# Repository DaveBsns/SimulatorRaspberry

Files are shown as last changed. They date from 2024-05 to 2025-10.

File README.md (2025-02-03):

# VR Bicycle Simulator Repository (HHN UniTyLab)

This Repo contains all Scripts to run the VR Bicylce Simulator in addtion to the Unity Project. 

## Hardware Sensor Overview

// IMAGE FROM BIKE SETUP

### Steering Sensor

<div style="display: flex; justify-content: space-evenly; align-items: center;">
  Steering Sensor Mount
  Handle Bar Mount
</div>

The image on the left shows the mount of the Photoelelectrical Encoder to measure the steering angle - the right images shows the handle bar from the front. There are two boxes on the top of the handle bar. In this image the left box contains the Mircocontroller (ESP32) for the brake and the right box contains the Microcontroller (ESP32) for the Steering sensor.

### Brake Sensor

<div style="display: flex; justify-content: space-evenly; align-items: center;">
  Steering Sensor Mount
  Handle Bar Mount
  Handle Bar Mount
</div>

Currently only the right hand brake is equipped with a sensor. The full setup is shown on the left image. The center images shows the mount of the hall sensor on the brake lever. If the brake sticks or does not work properly - make sure to check both screws are tight. 
The image on the right show the brake-block mounted in the V-brake - this block ensures a more realistc feeling of the brake lever.

**Important:** Make sure that the LED-light of the switch of the box is On - otherwise the brake sensor will be running with an older version!

### Elite Rizer

<div style="display: flex; justify-content: space-evenly; align-items: center;">
  Steering Sensor Mount
</div>

The Elite Rizer is used to adjust the height of the front axis occording to the incline in the Simulation. Be aware that this component needs to find the Zero points when being started.

### Direto 

<div style="display: flex; justify-content: space-evenly; align-items: center;">
  Steering Sensor Mount
</div>

This component is responsible for measuring the speed of the pedals and adjusting the resistance of the pedals accourding to the incline in the simulation. 

### Roll 

<div style="display: flex; justify-content: space-evenly; align-items: center;">
  Steering Sensor Mount
</div>

This (white) roll can be used to move backwards with the bicycle in the simulation. To go backwards the roll has to be kicked forwards.

## Repository Overview

- **`archive/`**: Archived files and scripts.
  
- **`collector_scripts/`**: Main directory for scripts handling data collection and Sensor scripts.
  
  - **`sensor_scripts/`**: Each Subdirectory contains a PlatformIO project - one for each mircocontroller (ESP32) utilising a sensor for data collection of the Bicycle setup. 

    - **`Arduino_Files/`** ---
    - **`Brake_Sensor/`** Hall sensor mounted on left brake lever (indirect brake force)
    - **`Gyro_Sensor/`** BNO055 mounted on Rocker plate (measure tilting)
    - **`Roll_Sensor/`** Roll sensor (for backward movement on bicycle)
    - **`Steering_Sensor/`** Photoelectric encoder (steering Angle)

  - `direto_xr.py` Script utilising BLE for reading speed from direto and writing resitance of direto
  - `elite_rizer.py` Script utilising BLE for writing front wheel height
  - `headwind.py` Script utilising BLE for writing headwind speed
  - `master_collector.py` Scripct for collecting data from microcontrollers (UDP) and sending data to Unity (UDP)
  - `master_receiver.py` Script for recieving data from Unity (UDP)
  - `p110_connect.py` Script for controlling smart plug (power supply for bicycle setup)
  - `UDP_tester.py` Srcipt for testing UDP functionality
  - `run_scripts.bat`: Batch script for running all scripts.

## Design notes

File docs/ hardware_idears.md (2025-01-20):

- Foot sensor while stand still Structure-borne sound transducer maybe with light barrier or pressure sensor
- Structure-borne sound transducer for undergound feedback and crashes (rockhorn)
- Brake feedback (maybe with pressure sensor)

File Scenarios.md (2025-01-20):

# Scenarios Bicycle Simulator

Parts of several use cases are combined into a scenario.

Scenario 1: Easy ride in the city
* Good weather
* Bicycle lane is free
* Cars keep their distance
* Cars don’t drive too fast
* Intersection with a red light that the cyclist crosses straight 
* Stop sign at intersection with traffic lights
* During the day
* Covers 15 Use Case Actions

Scenario 1b: Cycling on inclined slopes
* Ride in the parking garage
* no use case, just to test the Elite Rizer

Scenario 2: Difficult ride in the city
* Good weather
* Construction site on the bicycle lane
* Cars blocking the bicycle lane
* Fast traffic and close cars passes
* High traffic density
* Left turn incl. turning lane and traffic light
* Intersection without traffic lights and „Vorfahrt gewähren“ sign
* Zebrastreifen (Pedestrian crossing)
* Sun sets
* Covers 18 Use Case Actions

Scenario 3: Dangerous ride in the city
* Obstacles on the ground, narrow points
* Slow cyclists
* Cars drive fast and way too close
* Bad parking
* There is a „Vorfahrt“ intersection, but a car takes the right of way
* Covers 5 Use Case Actions

Scenario 4: Foggy night ride in the city
* Nighttime with lantern lights
* Cars pass by with headlights on
* Fog makes vision difficult
* Covers 6 Use Case Actions

Scenario 5: Adventure ride in the forest
* Hilly terrain
* Fog
* Forest
* Covers 4 Use Case Actions

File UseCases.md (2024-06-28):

# Use Cases Bicycle Simulator

## Use Case Overview

R1 - Removing barriers and building security

R2 - Expansion of driving practice (mainly on intersections)

R3 - Expansion of driving practice (mainly overtaking and narrow spots)

R4 - Expansion of driving practice at different times of the day

R5 - Weather influences when cycling

A1 - Building confidence on the bicycle path next to the road

A2 - Building confidence when driving on the road

A3.1 - Feeling safe when being overtaken by cars

A3.2 - Measuring stress when being overtaken by cars

A4 - Cycling at night and sharing the road with other cars

A5 - Cycling under varying weather conditions at varying times of day and at night

The individual cyclist actions are taken from the requirements document and named in alphabetical order.

## R1 - Removing barriers and building security

| Use Case Number | Description | Scenario | Direto | Rocker Plate | Brake | Rizer |
| --- | --- | --- | --- | --- | ----- | ----- |
| R1a | Getting on the bike | 1 | | x | | |
| R1b | Starting to ride the bike straight on even ground, no vehicles driving past | 1 | x | | | |
| R1b | Raising the right hand to indicate an upcoming turn to the right | 1 | x | x | | |
| R1b | Turning right | 2 | x | x | | |
| R1c | Raising the left hand to indicate an upcoming turn to the left | 2 | x | x | | |
| R1c | Turning left | 2 | x | x | | |
| R1d | Driving uphill | 5 | x | | | x |
| R1d | Driving downhill | 5 | x | | (x) | x |
| R1e | Riding around obstacle on the floor | 3 | x | x | | |
| R1f | Hitting the brakes hard because of a dangerous situation | 3 | | | x | |

## R2 - Expansion of driving practice (mainly on intersections)

| Use Case Number | Description | Scenario | Direto | Rocker Plate | Brake | Rizer |
| --- | --- | --- | --- | --- | ----- | ----- |
| R2a | Cyclist starts riding at an intersection | 1 | x | | | |
| R2b | Cyclist stops for a red traffic light | 1 | | | x | |
| R2c | Right turn indication and execution at an intersection | 2 | x | x | | |
| R2c | Left turn indication and execution at an intersection | 2 | x | x | | |
| R2d | Getting into the turning lane | 2 | x | x | x | |
| R2e | Traffic signs at intersections: Stop, Vorfahrt, Vorfahrt gewähren | 1/2/3 | x | | x | |

##

## R3 - Expansion of driving practice (mainly overtaking and narrow spots)

| Use Case Number | Description | Scenario | Direto | Rocker Plate | Brake | Rizer |
| --- | --- | --- | --- | --- | ----- | ----- |
| R3a | Driving past parked car (regular parking) | 1 | x | | | |
| R3a | Driving past parked car (bad parking going into the bicycle lane) | 2 | | | x | |
| R3b | Overtaking other cyclists | 3 | x | x | | |
| R3c | Driving through a narrow point | 3 | x | (x) | (x) | |

## R4 - Expansion of driving practice at different times of the day

| Use Case Number | Description | Scenario | Direto | Rocker Plate | Brake | Rizer |
| --- | --- | --- | --- | --- | ----- | ----- |
| R4a | Driving at dusk | 2 | x | | | |
| R4b | Driving during the night | 4 | x | | | |

## R5 - Weather influences when cycling

| Use Case Number | Description | Scenario | Direto | Rocker Plate | Brake | Rizer |
| --- | --- | --- | --- | --- | ----- | ----- |
| R5a | Driving on wet road | - | x | | | |
| R5b | Driving in rain | - | x | | | |
| R5b | Driving in fog | 4 | x | | | |
| R5c | Driving in snow and slippery conditions | - | x | x | | |
| R5c | Driving in snow and slippery conditions on a bridge | - | x | x | | |
| R5d | Braking for an obstacle visible only late because of bad weather conditions | 5 | | | x | |
| R5d | Braking in slippery weather conditions | - | | x | x | |
| R5e | Driving at night —> see no difference to R4b | 4 | x | | | |
| R5f | Driving in the city with poor visibility | 4 | x | | | |
| R5f | Driving in the forest with poor visibility | 5 | x | | | |

## A1 - Building confidence on the bicycle path next to the road

| Use Case Number | Description | Scenario | Direto | Rocker Plate | Brake | Rizer |
| --- | --- | --- | --- | --- | ----- | ----- |
| A1a | Being overtaken by passing cars in low traffic density | 1 | x | | | |
| A1a | Being overtaken by passing cars in high traffic density | 2 | x | | | |
| A1b | Being overtaken by passing cars with low speed | 1 | x | | | |
| A1b | Being overtaken by passing cars with high speed | 2 | x | | | |
| A1c | Crossing an intersection with low traffic density and traffic lights | 1 | x | | x | |
| A1c | Crossing an intersection with high traffic density and regular road crossing | 2 | x | | x | |

##

## A2 - Building confidence when driving on the road

| Use Case Number | Description | Scenario | Direto | Rocker Plate | Brake | Rizer |
| --- | --- | --- | --- | --- | ----- | ----- |
| A2a | Driving on the road, no bike path, low traffic density, slow cars | 1 | x | | | |
| A2a | Driving on the road, no bike path, high traffic density, fast cars | 2 | x | | | |
| A2bde | Approaching an intersection with cars, right turn incl. turning lane | 1 | x | x | x | |
| A2bde | Approaching an intersection with cars, left turn incl. turning lane  | 2 | x | x | x | |
| A2c | Stopping at traffic lights | 1 | | | x | |

##

## A3.1 - Feeling safe when being overtaken by cars

| Use Case Number | Description | Scenario | Direto | Rocker Plate | Brake | Rizer |
| --- | --- | --- | --- | --- | ----- | ----- |
| A3a | Being overtaken by a car with usual distance | 1 | x | | | |
| A3a | Being overtaken by a close car | 2 | x | | | |
| A3b | Being overtaken by a slow car (combine with A2a) | 1 | x | | | |
| A3b | Being overtaken by a fast car (combine with A2a) | 2 | x | | | |
| A3c | Being overtaken by a fast car with obstacles on the side | 2 | x | | x | |

##

## A4 - Cycling at night and sharing the road with other cars

| Use Case Number | Description | Scenario | Direto | Rocker Plate | Brake | Rizer |
| --- | --- | --- | --- | --- | ----- | ----- |
| A4a | Driving at dusk with car headlights behind you or in oncoming traffic  | 2 | x | | | |
| A4b | Driving at night with car headlights behind you or in oncoming traffic | 4 | x | | | |

##

## A5 - Cycling under varying weather conditions at varying times of day and at night

| Use Case Number | Description | Scenario | Direto | Rocker Plate | Brake | Rizer |
| --- | --- | --- | --- | --- | ----- | ----- |
| A5a | Driving on a wet road with cars next to it | - | x | | | |
| A5b | Driving in rain/fog or poor visibility including car headlights | 4 | x | | | |
| A5c | Driving in snow and slippery conditions, possibly with splashing slush | - | x | | | |
| A5d | Driving in different weather conditions at dusk and at night | - | x | | | |

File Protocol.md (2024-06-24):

Thursday, 21st March 2024:
- We're going to use a Miroboard for brainstorming (PB)
- Github issues for Task management
- Markdown for documentation
- Road runner license (DF)
- Demo: Booting up the simulator in the lab (DF)
- Basic workflow - work on the personal laptop, push the code, test in the lab, then merge successfully implemented features (DF)

Thursday, 28th March 2024:
- Determine whether to use Roadrunner or just Unity for VR editing using the following questions
1. What looks better?
2. What's easier to implement?
3. Do we have German roads, street signs and bicycle lanes?
- Overview of Unity version control
- Overview of sensor collection scripts
- Discussion of the steering logic: can be improved, but this isn't required in this project

Thursday, 11th April 2024:
- Preparation for intermediate presentation scheduled for April 18

Monday, 6th of May 2024:
- Pooja is working on lighting during the day
- Philipp Baumann is working on traffic lights
- Philipp Senfft is working on the Rizer
- Marc Hessenauer is working on the cars
- sync for presentation on May 16th
- agreement on parking garage as the next test area for incline
- agreement on slight adaption of the scenarios 2,3 and 4
- discussion on whether we will write a paper or a non-scientific documentation

Thu, 30 May 2024

Current State Overview
- Scenario 1: Complete and functional.
- Scenario 1b: Implementation on Unity side is complete; testing on the simulator is pending.
- Scenario 2 & 3 Concepts: Conceptualization is complete.
- Scenario 3: Philipp has begun implementation in Unity.
- Scenario 2: Pooja has begun implementation in Unity.

Goal for End of Semester
- Scenario 1: Ensure it is fully functional, including Scenario 1b to demonstrate a working Rizer.
- Scenario 2: Complete implementation, excluding weather conditions.
- Scenario 3: Complete implementation, excluding weather conditions and limited to basic physics for slow bicyclists.
- Documentation: Prepare and possibly finalize a paper or documentation of the project.

Thu, 6 June 2024: 

Current State Overview:
- Scenario 1: Complete & functional
- Scenario 1b: Work in Progress: Demonstraiting Incline (ajust Rizer)
- Scenario 2: (no new update because pooja could not attend meeting)
- Scenario 3: Scenario in Unity created with assets (wip: way point bike controller & missing: car takes the right of way)

Goal for End of Semester (27.6): 
- same goals as from 30 May 2024
- additional adjust the durito for incline demonstation
- Documentation: Write documentation of the project (not paper) until 5.7, latest 26.7.

Thu, 13 June 2024:
  
  Scenario 2: Work in Progress
  
  Scenario 3:
    - Done: WayPointBike slow self driving on bike lane
    - Work in Progress: Cars taking right of way
  
  Rizer: 
    - issue: DataReceiver has inconsistent values in calls variables.
  
  Documentaion:
    - inital draft of Structure missing additional Chapter of Project Structure (For others to know how to work on project in the future)
    
  Presentation: 
    - Goal 15 minutes (max 20 with demonstration)
    - Marc will create inital draft of presentation until next week

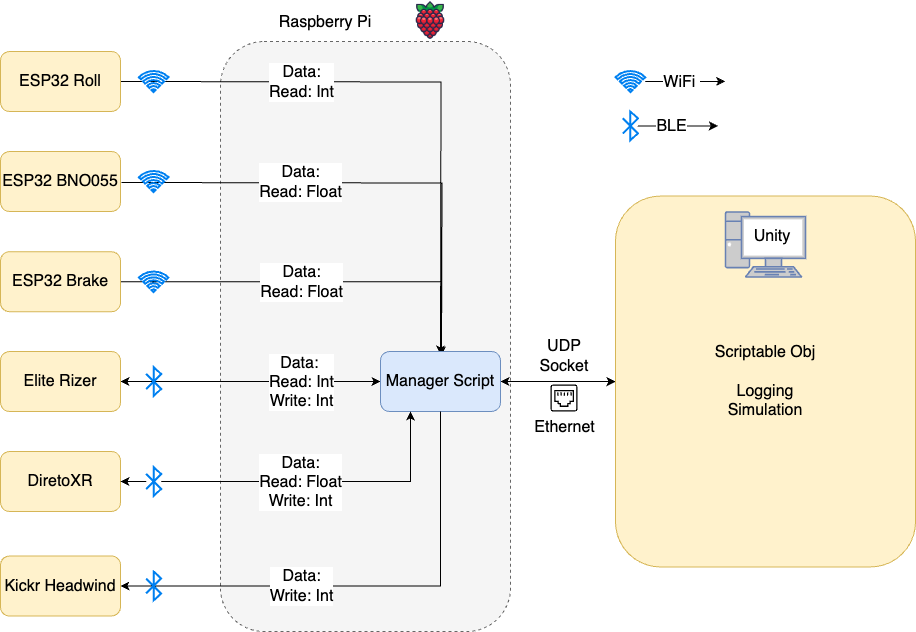
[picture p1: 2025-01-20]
Architecture_BicycleSimulator.drawio.png

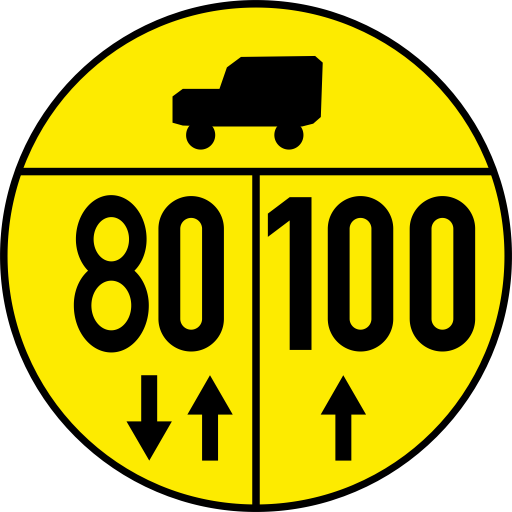
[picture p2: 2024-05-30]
roadrunner/signs/special_signs/Sign_I_1.png

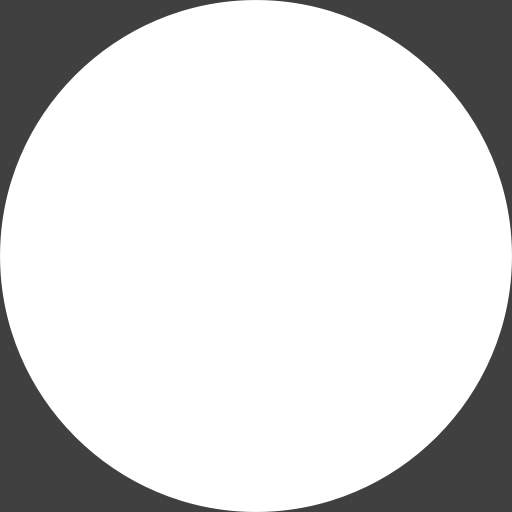
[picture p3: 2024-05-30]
roadrunner/signs/special_signs/Sign_I_1-Back.png

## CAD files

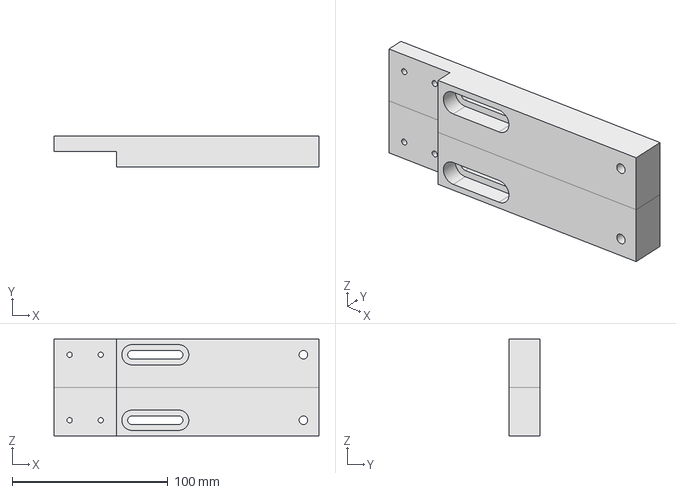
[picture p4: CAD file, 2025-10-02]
hardware/backward_motion_input/baseB.FCStd
170.0 x 20.0 x 62.0 mm

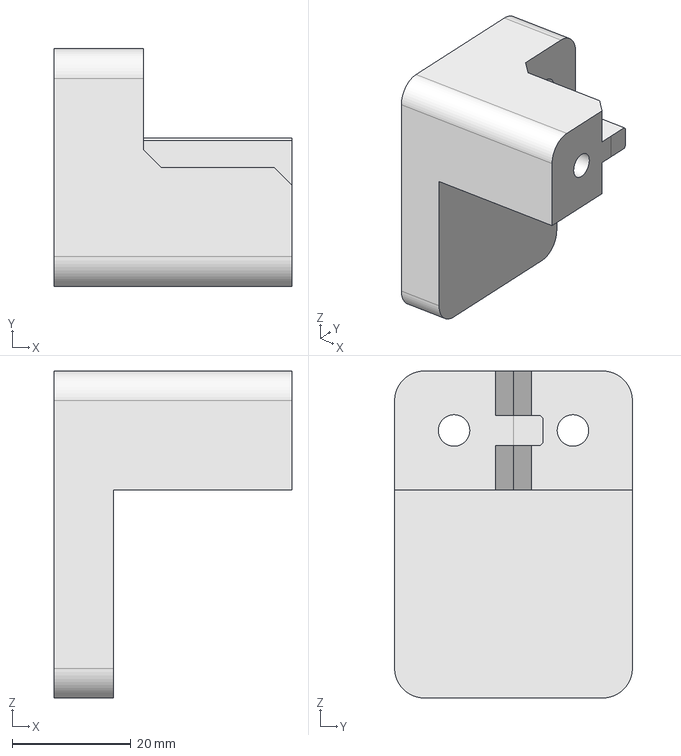
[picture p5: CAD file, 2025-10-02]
hardware/backwheel_and_pedal_sensor/backwheel_sensor_mount/clampJawA.FCStd
40.0 x 40.0 x 55.0 mm

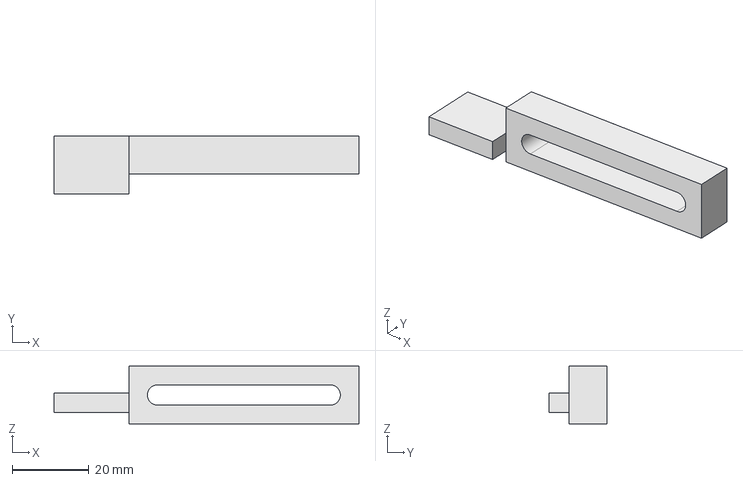
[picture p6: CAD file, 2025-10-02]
hardware/backwheel_and_pedal_sensor/sensorMountBackWheelAndPedal.FCStd
79.5 x 15.2 x 15.0 mm

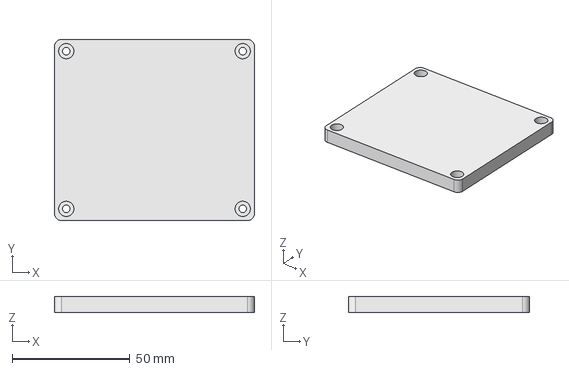
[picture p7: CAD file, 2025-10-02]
hardware/gyro_roll_sensor/GyroRollBoxLidStep.step
85.0 x 77.0 x 7.00 mm

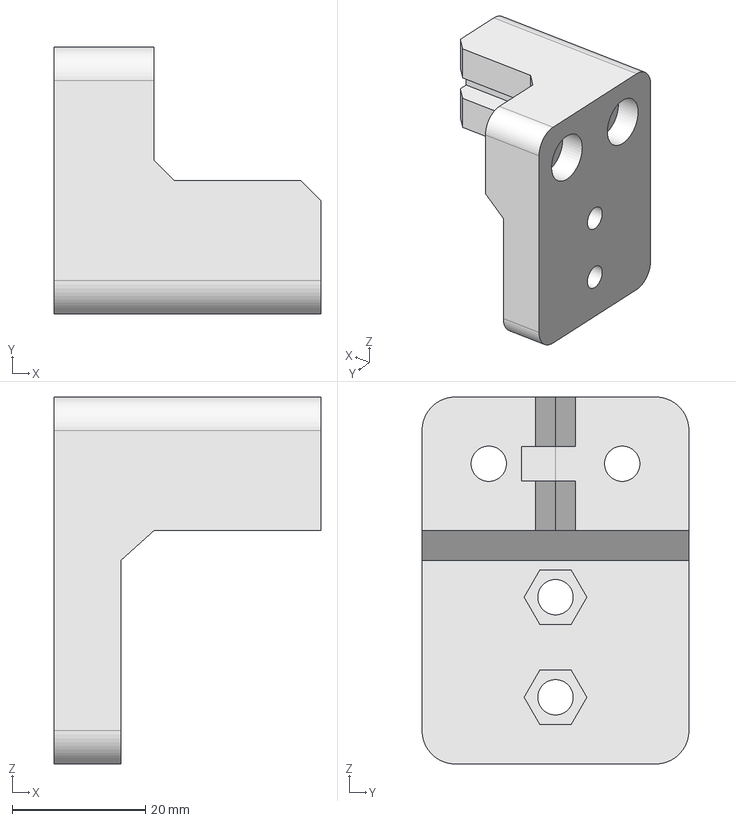
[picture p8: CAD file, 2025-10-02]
hardware/backwheel_and_pedal_sensor/backwheel_sensor_mount/clampJawB.FCStd
40.0 x 40.0 x 55.0 mm

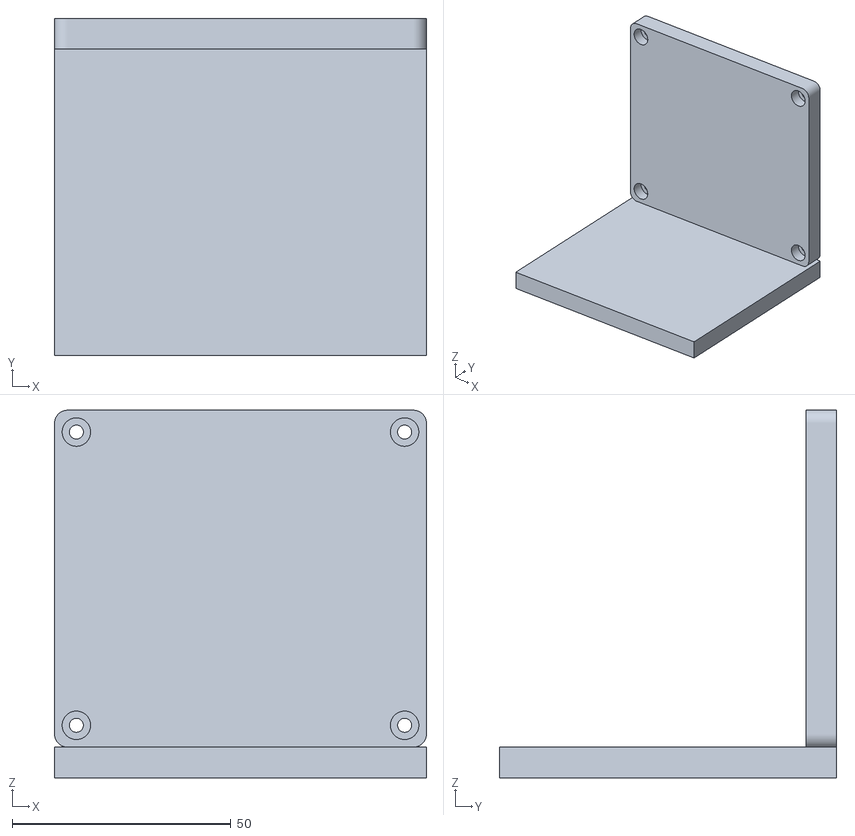
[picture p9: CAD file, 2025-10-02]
hardware/gyro_roll_sensor/GyroRollBoxLidStl.stl
85.0 x 77.0 x 84.0

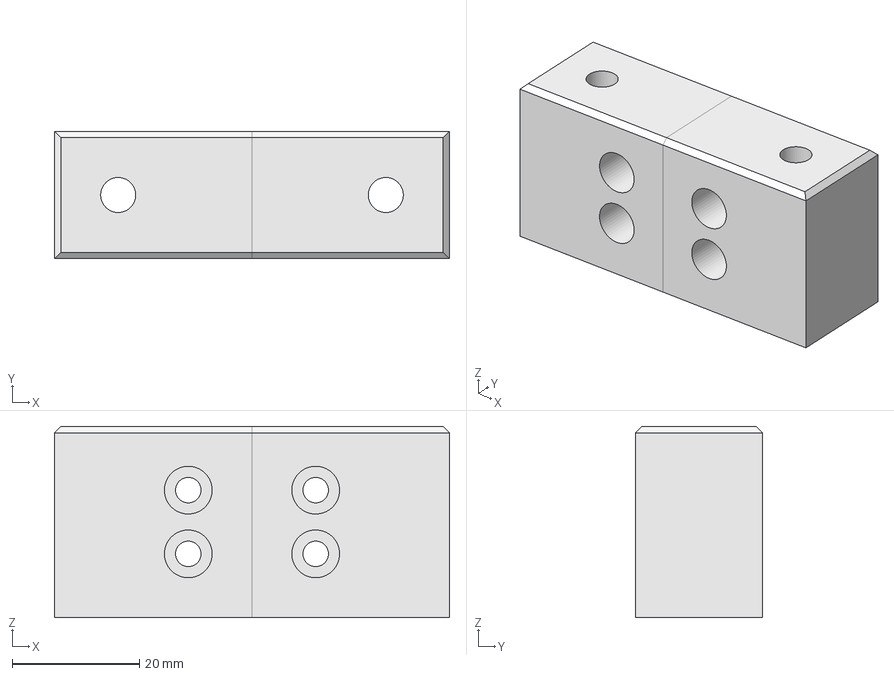
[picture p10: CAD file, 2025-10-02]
hardware/backward_motion_input/mountBoxConnectorStep.step
62.0 x 20.0 x 30.0 mm

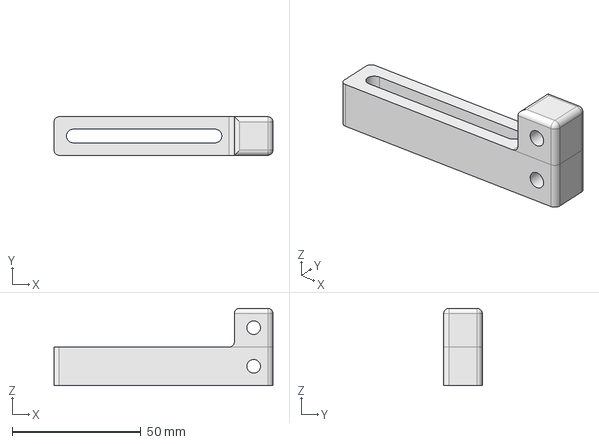
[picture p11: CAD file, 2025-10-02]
hardware/backwheel_and_pedal_sensor/backwheel_sensor_mount/connector1step.step
85.0 x 15.0 x 30.0 mm

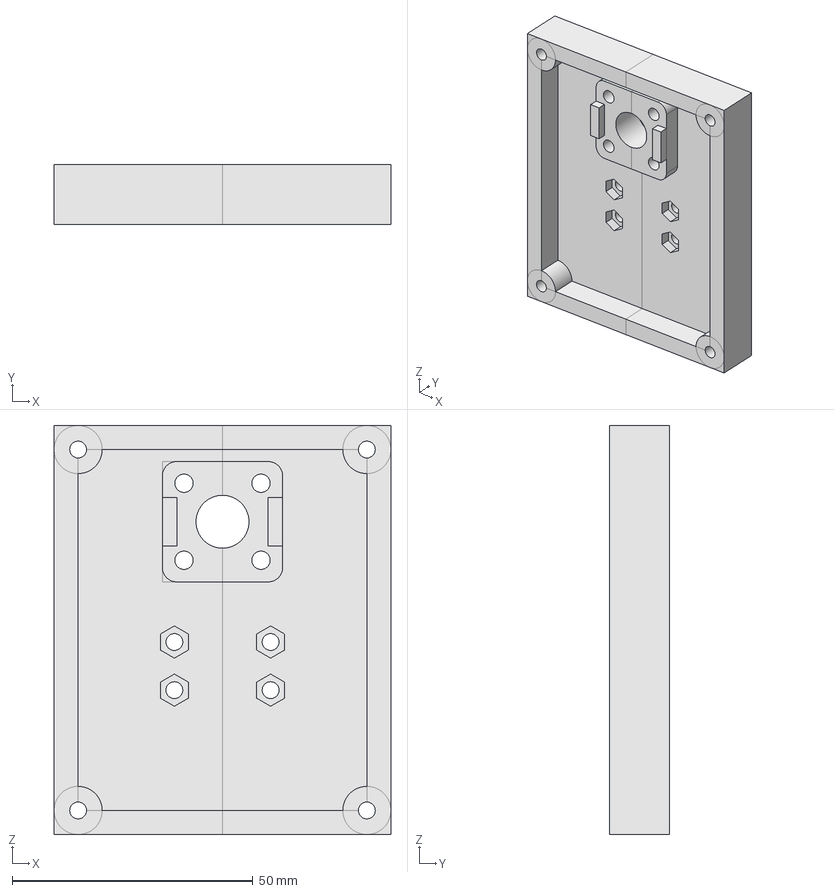
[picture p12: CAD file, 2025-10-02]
hardware/backward_motion_input/backwardMotionInputSensorBox.FCStd
70.0 x 12.5 x 85.0 mm

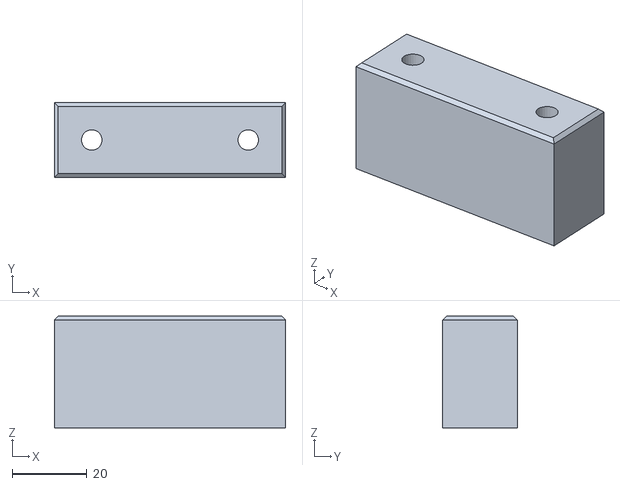
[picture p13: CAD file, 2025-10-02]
hardware/backward_motion_input/mountBasicStl.stl
62.0 x 20.0 x 30.0

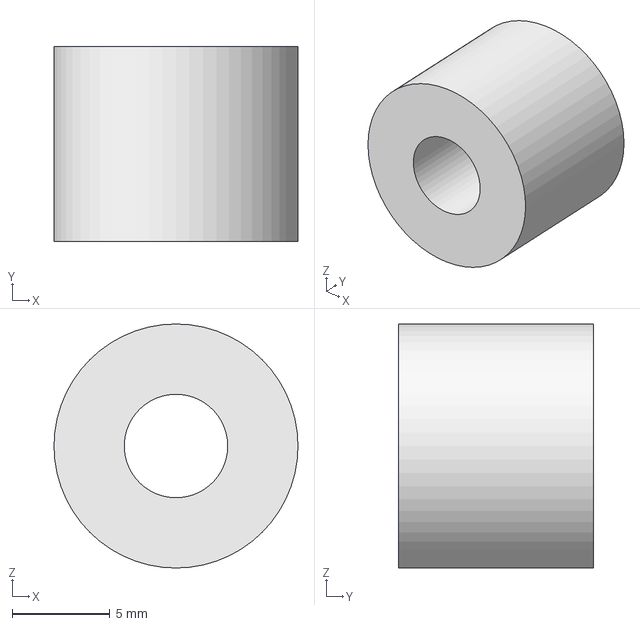
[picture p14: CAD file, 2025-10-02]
hardware/backwheel_and_pedal_sensor/backwheel_sensor_mount/spacer.FCStd
12.5 x 10.0 x 12.5 mm

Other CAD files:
hardware/backward_motion_input/baseBStl.stl
hardware/backwheel_and_pedal_sensor/sensorMountBackwheelAndPedalstep.step
hardware/backwheel_and_pedal_sensor/backwheel_sensor_mount/clampJawAstl.stl
hardware/backwheel_and_pedal_sensor/sensorMountBackwheelAndPedalstl.stl
hardware/gyro_roll_sensor/GyroRollBoxLid.FCStd
hardware/backward_motion_input/baseBStep.step
hardware/backwheel_and_pedal_sensor/backwheel_sensor_mount/connector1stl.stl
hardware/backward_motion_input/backwardMotionInputSensorBoxLid.FCStd
hardware/backward_motion_input/backwardMotionInputSensorBoxLidStep.step
hardware/backward_motion_input/backwardMotionInputSensorBoxLidStl.stl
hardware/backward_motion_input/backwardMotionInputSensorBoxStl.step
hardware/backward_motion_input/backwardMotionInputSensorBoxStl.stl
hardware/backward_motion_input/baseA.FCStd
hardware/backward_motion_input/baseAStep.step
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

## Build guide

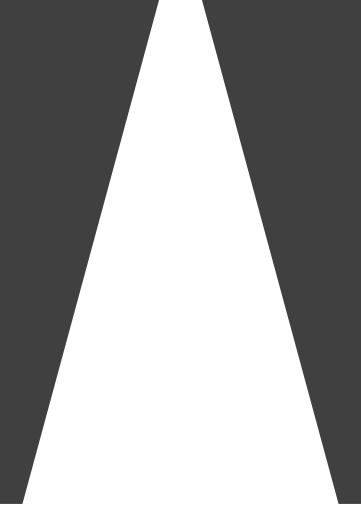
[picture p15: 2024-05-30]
roadrunner/signs/traffic_installations/Sign_610-Back.png

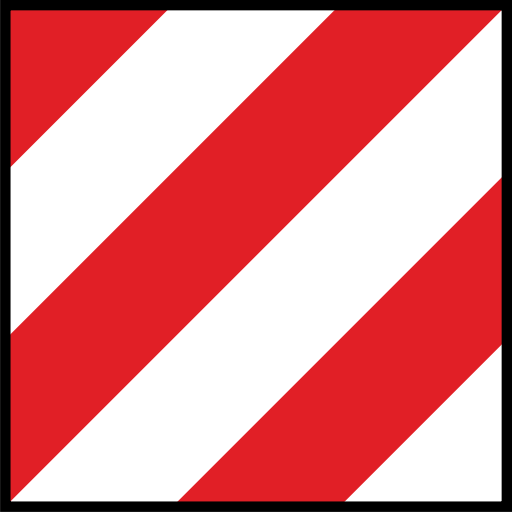
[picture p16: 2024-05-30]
roadrunner/signs/traffic_installations/Sign_630.png

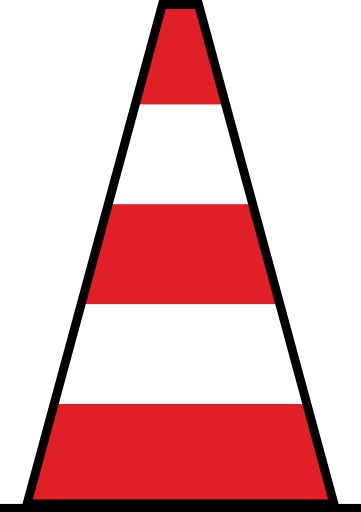
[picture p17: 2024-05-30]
roadrunner/signs/traffic_installations/Sign_610.png

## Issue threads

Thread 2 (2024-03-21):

Reverse engineer Rizer elite

PSenfft, 2024-03-21:
Sniff GATT Packages between smartphone app and rizer elite

- [x] read the BT LE introduction https://learn.adafruit.com/introduction-to-bluetooth-low-energy/introduction
- [x] use the nrf sniffer with wireshark and try if we can read the packages when two other devices are connected (try if its encrypted)
- [x] create API to change the tilt
- [x] change the while loop and read steering method to decrease the lag to write the tilt (maybe own thread)
- [x] test everything

unitylab-dev, 2024-03-21:
BT Notes
Filtering BT devices by advertising number in Wireshark (Rizer Elite)
btle.advertising_address == fc:12:65:28:cb:44

unitylab-dev, 2024-03-21:
First try to sniff connection between smartphone and Rizer Elite.
SCN_REQ and SCAN_RSP is probably the interesting stuff
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

unitylab-dev, 2024-03-21:
Mybe usefull links
https://devzone.nordicsemi.com/nordic/nordic-blog/b/blog/posts/one-minute-to-understand-ble-connection-data-packa
https://www.bluetooth.com/blog/bluetooth-low-energy-it-starts-with-advertising/

unitylab-dev, 2024-03-28:
https://devzone.nordicsemi.com/guides/short-range-guides/b/bluetooth-low-energy/posts/ble-characteristics-a-beginners-tutorial

PSenfft, 2024-04-11:
BT debugging log from Android Smartphone when I change the value of the rizer with the App.

[btsnoop_hci.log](https://github.com/DaveBsns/SimulatorRaspberry/files/14945539/btsnoop_hci.log)

PSenfft, 2024-04-12:
Here is the BT debugging log again. Connection between my Android Phone (Google Pixel 7) between the Elite Rizer. I changed the Value to the maximum (20% gradient) to the minimum. After that, I connected with the Headwind device and changed the speed manual (with the buttons on the device) from the lowest to the highest value

[btsnoop_hci.log](https://github.com/DaveBsns/SimulatorRaspberry/files/14957967/btsnoop_hci.log)

pooja0973, 2024-04-12:
I was able to replicate till here but I am facing issue while connecting IOS phone.
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

PSenfft, 2024-04-13:
I think we don't need the nrf sniffer. I got better results with the log files from my phone.
when you use the filter btatt.opcode == 0x12 in wireshark, when you open my last log files you can see we have package 472-482 with different Handle code. I think that's a handshake or something like that.
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

and after that, we have just two different packages. The first one to increase the gradient and the second package typ to decrease the gradient. Just like in the app with + and -
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

This Hex Stream should be the value for up:
060102
and this for down:
060402

marc-hessenauer, 2024-05-16:
Nicely done!! Is this issue still open?

marc-hessenauer, 2024-05-20:
Alright! Narrowed down the issue to just one assignee as this reflects the current state of work distribution

Closed 2024-07-03.

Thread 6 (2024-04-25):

Don't turn camera when steering

unitylab-dev, 2024-04-25:
Currently the camera moves with the direction of the bicycle, even when the head with the VR Headset is still

marc-hessenauer, 2024-05-22:
Setting to edit: Road Users > VRBicycle Start > [CameraRig] > Object Follower > Object To Follow

marc-hessenauer, 2024-06-07:
was re-evaluated and is now closed due to low priority. parameter given above was already set to a suitable property

Closed 2024-06-07.

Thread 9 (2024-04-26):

Add terrain

marc-hessenauer, 2024-04-26:
add an extra section with terrain (up/down) that's accessible by bike

marc-hessenauer, 2024-06-24:
implement the following use case:
* Driving in the forest with poor visibility

marc-hessenauer, 2024-06-26:
Scenario 5 hab incline, poor visibility still missing

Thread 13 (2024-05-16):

Add dangerous car drivers #scenario2

marc-hessenauer, 2024-05-16:
Cars stop very late for bicycles

marc-hessenauer, 2024-05-21:
Added two flags:
BadDriver has a narrow Raycast range, meaning bicycles are detected late in curves
FastDriver has a maximum speed of 20, which is very high for current maps

These flags can be set on any car

Closed 2024-05-21.

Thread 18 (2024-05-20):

Draft and adapt scene for #scenario3

marc-hessenauer, 2024-05-20:
Scenario 3: Dangerous ride in the city

- Bad weather: rain and wet roads
- Obstacles on the ground, narrow points
- Nighttime
- Slow cyclists
- Cars drive fast and way too close
- Bad parking
- There is a „Vorfahrt“ intersection, but the car takes the right of way
- Covers 14 Use Case Actions

Goal of this issue:
- [ ] Draft the Scene in Miro, double check with a teammate if this reflects the scenario
- [ ] Copy Scene 1 and rename the new scene to "Scene 3"
- [ ] Add obstacles as defined in the scenario description
- [ ] create issues for other todos in this scene, should they not exist yet

Closed 2024-06-22.

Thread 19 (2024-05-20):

Draft and adapt scene for #scenario4

marc-hessenauer, 2024-05-20:
Scenario 4: Fun adventure ride in the forest
- Hilly terrain
- Fog, snow, slippery conditions
- Crossing a windy bridge with slippery ground
- Outside the city
- 8 Use Case Actions
- Fun ideas: Animals crossing the path, obstacles on the way etc.

Goal of this issue:
- [ ] Draft the Scene in Miro, double check with a teammate if this reflects the scenario
- [ ] Create scene
- [ ] Create issues for other todos in this scene, should they not exist yet

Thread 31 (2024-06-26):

Implement Direto and resistance

PSenfft, 2024-06-26:
Direto API is already finished. Data transmission from unity to direto API is missing.

PSenfft, 2024-06-26:
[Resistance_snippet.md](https://github.com/user-attachments/files/15985952/Resistance_snippet.md)

Closed 2024-07-01.

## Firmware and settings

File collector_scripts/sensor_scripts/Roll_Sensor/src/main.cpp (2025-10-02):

#include <Arduino.h>
#include <Wire.h>
#include <WiFi.h>
#include <WiFiUdp.h>
#include <ArduinoJson.h>

const int HALL_PIN = 32;

//const char* ssid = "raspi-webgui";
//const char* password = "bikingismylife";
const char *ssid = "Bicycle_Simulator_Network";
const char *password = "17701266";
unsigned int localUdpPort = 6666;
const unsigned long udpSendInterval = 500; // Interval for sending UDP packets in milliseconds
unsigned long lastUdpSendTime = 0; // Variable to store the last time UDP packet was sent

WiFiUDP udp;

using namespace std;  // Use the std namespace for ArduinoSTL

// General control settings and flags
const int debugging = 0;
const int printResult = 1;
const int directionalMode = 1;

// Control timings in ms
const int loopTime = 60; // time between value calculation and printing in average angle reading
const int iterationCount = 20; // how many angle readings to average in one loop
const int iterationPadding = 0; // time between individual value readings

// Control settings for turn direction reading
const float turnSensitivityActivation = 6; // default: 22 - for turn direction
const float turnSensitivityDeactivation = 31;

// AS5600 device specifics
const int deviceAddress = 0x36;
const int registerAddressHigh = 0x0E; // Register for high 4 bits
const int registerAddressLow = 0x0F;  // Register for low 8 bits
const int maxSensorValue = 4095;
const int maxDegrees = 360;
const int SDA_PIN = 18;
const int SCL_PIN = 19;

// Reused variables
unsigned long loopStartTime;
unsigned long loopEndTime;
unsigned long executionTime;
float lastReadAngle = 0;
int directionBufferIndex = 0;
int directionBufferSize = 0;
uint64_t directionBuffer = 0;
int turnDirection = 0;
int lastTurnDirection = 0;
int nextBit = 0;
int angleTolerance = 0;
int readValues = 0;

// ==== Function declarations (prototypes) ====
void AddToBuffer(int val);
int countOnes(uint64_t n);
void printBufferBits();
void averageAngle();
void getRotation();
float readAngle();
double meanAngle(const float angles[], int size);
void printArray(const float arr[], int size);

// ==== Setup and loop ====
void setup() {
  Wire.begin(SDA_PIN, SCL_PIN);
  Serial.begin(115200);

  WiFi.hostname("Roll_ESP");
  WiFi.begin(ssid, password);

  while (WiFi.status() != WL_CONNECTED)
  {
    delay(1000);
    Serial.print("Connecting with WiFi with ssid: ");
    Serial.print(ssid);
    Serial.print(" and password: ");
    Serial.println(password);
    Serial.println(WiFi.status());
  }

  Serial.println("Connection with WiFi successful");
  udp.begin(localUdpPort);

  loopStartTime = millis();
}

void loop() {
  if (directionalMode) {
    getRotation();
  } else {
    averageAngle();
  }

  // Check if it's time to send the UDP packet
  unsigned long currentTime = millis();
  if (currentTime - lastUdpSendTime >= udpSendInterval) {
    StaticJsonDocument<500> doc;

    String jsonStr;
    doc["sensor"] = "AS5600";
    doc["sensor_value"] = turnDirection;

    serializeJson(doc, jsonStr);

    // Read UDP messages
    int packetSize = udp.parsePacket();
    if (packetSize) {
      char packetBuffer[255];
      udp.read(packetBuffer, packetSize);

      Serial.print("Received message: ");
      Serial.println(packetBuffer);
    }

    udp.beginPacket("192.168.0.101", 6666);
    udp.print(jsonStr);
    udp.endPacket();

    // Update the last send time
    lastUdpSendTime = currentTime;
  }
}

// ==== Function definitions ====

void AddToBuffer(int val) {
  directionBuffer = (directionBuffer << 1) | (val & 1);
}

int countOnes(uint64_t n)
{
  unsigned int c;
  for (c = 0; n; n = n & (n-1)) {
    c++;
  }
  return c;
}

void printBufferBits() {
  for (int i = 63; i >= 0; i--) {
    uint64_t bit = (directionBuffer >> i) & 1;
    Serial.print((int)bit);
  }
  Serial.println();
}

void averageAngle() {
  loopStartTime = millis();
  float angleReadings[iterationCount];

  for (int it = 0; it < iterationCount; ++it) {
    float angle = readAngle();
    if (isnan(angle)) {
      Serial.print(" !Reading Error! ");
      continue;
    }
    angleReadings[it] = angle;
    if (iterationPadding > 0) delay(iterationPadding);
  }

  int readValuesSize = sizeof(angleReadings) / sizeof(angleReadings[0]);
  float averagedAngle = meanAngle(angleReadings, readValuesSize);

  if (debugging) {
    Serial.println("");
    Serial.print("Raw values: ");
    Serial.println(readValuesSize);
    printArray(angleReadings, readValuesSize);
  }

  if (printResult) {
    Serial.print("Angle: ");
    Serial.println(averagedAngle, 3);
  }

  loopEndTime = millis();
  executionTime = loopEndTime - loopStartTime;

  if (debugging) {
    Serial.print("execution time: ");
    Serial.println(executionTime);
  }

  if (executionTime <= loopTime) {
    delay((float)(loopTime - executionTime));
  } else {
    if (debugging) {
      Serial.println("Cant keep up! Execution time of " + (String)executionTime + "ms is " + (String)(executionTime - loopTime) + "ms over the budget!");
    } else {
      Serial.println(" Device Slowdown!");
    }
  }
}

float readAngle() {
  Wire.beginTransmission(deviceAddress);
  Wire.write(registerAddressHigh);
  int transmissionStatusHigh = Wire.endTransmission();
  if (transmissionStatusHigh != 0) {
    Serial.print("Error in I2C transmission (high byte). Status: ");
    Serial.println(transmissionStatusHigh);
    return NAN;
  }

  Wire.requestFrom(deviceAddress, 1);
  while (Wire.available() < 1);
  byte highByte = Wire.read();

  Wire.beginTransmission(deviceAddress);
  Wire.write(registerAddressLow);
  int transmissionStatusLow = Wire.endTransmission();
  if (transmissionStatusLow != 0) {
    Serial.print("Error in I2C transmission (low byte). Status: ");
    Serial.println(transmissionStatusLow);
    return NAN;
  }

  Wire.requestFrom(deviceAddress, 1);
  while (Wire.available() < 1);
  byte lowByte = Wire.read();

  int sensorValue = (highByte << 8) | lowByte;
  float degrees = (float(sensorValue) / maxSensorValue) * maxDegrees;
  if (degrees == 360.0) degrees = 0.0;

  readValues++;
  return degrees;
}

double meanAngle(const float angles[], int size) {
  double x = 0.0;
  double y = 0.0;
  for (int i = 0; i < size; ++i) {
    x += cos(angles[i] * PI / 180);
    y += sin(angles[i] * PI / 180);
  }
  return (atan2(y, x) * 180 / PI) + 180;
}

void printArray(const float arr[], int size) {
  Serial.print("[");
  for (int i = 0; i < size; ++i) {
    Serial.print(arr[i], 3);
    if (i < size - 1) Serial.print(", ");
  }
  Serial.println("]");
}

void getRotation() {
  float newAngle = readAngle();
  if (newAngle > lastReadAngle + angleTolerance) {
    AddToBuffer(1);
  } else if (newAngle < lastReadAngle - angleTolerance) {
    AddToBuffer(0);
  } else {
    nextBit = (nextBit + 1) % 2;
    AddToBuffer(nextBit);
  }

  lastReadAngle = newAngle;

  int ones = countOnes(directionBuffer);
  int zeroes = 64 - ones;

  if (debugging) {
    Serial.println("Zeroes count: " + (String)zeroes + ", Ones count: " + (String)ones + ".");
  }

  int sensitivity = (lastTurnDirection == -1 || lastTurnDirection == 1)
                      ? turnSensitivityDeactivation
                      : turnSensitivityActivation;

  if (ones > 64 - sensitivity) turnDirection = 1;
  else if (ones <= sensitivity) turnDirection = -1;
  else turnDirection = 0;

  if (printResult && lastTurnDirection != turnDirection) {
    lastTurnDirection = turnDirection;
    if (turnDirection == 1) Serial.println("Turning clockwise...");
    else if (turnDirection == -1) Serial.println("Turning counter-clockwise...");
    else if (turnDirection == 0) Serial.println("Not turning...");
  }

  if (millis() - loopStartTime > 10000) {
    Serial.println("Rate of " + (String)(readValues / 10) + " values per second.");
    loopStartTime = millis();
    readValues = 0;
  }
}

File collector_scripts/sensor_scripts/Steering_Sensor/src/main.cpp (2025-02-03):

#include <Arduino.h>
#include <WiFi.h>
#include <WiFiUdp.h>
#include <ArduinoJson.h>

#define A_PHASE 21
#define B_PHASE 22

// Variables for tracking the relative position of the encoder
volatile int position = 0;  // Encoder position
unsigned int flagA = 0;  // Counter for Counter-Clockwise (CCW) direction
unsigned int flagB = 0;  // Counter for Clockwise (CW) direction

// Encoder specifications and derived calculations
const float pulses_per_rev = 600.0;  // Encoder pulses per revolution (600 P/R)
const float degrees_per_pulse = 360.0 / (pulses_per_rev * 4);  // Quadrature decoding increases resolution by 4x

// Wi-Fi credentials for connecting to the VR setup network
const char *ssid = "Bicycle_Simulator_Network";
const char *password = "17701266";

// UDP configuration
unsigned int localUdpPort = 8778;  // Local UDP port for sending data
float angle = 0;  // Current calculated steering angle

WiFiUDP udp;

// Variables for tracking the encoder's quadrature decoding state
volatile int lastAState = 0;
volatile int lastBState = 0;

// Hysteresis filter threshold and timing configuration
const float hysteresisThreshold = 1.2;  // Minimum change in degrees to update
float lastAngle = 0.0;  // Last reported angle to avoid unnecessary updates
unsigned long previousMillis = 0;
const unsigned long interval = 50;  // Interval (ms) for sending updates over UDP

// Interrupt Service Routine (ISR) for handling encoder quadrature decoding
void IRAM_ATTR updateEncoder() {
  int AState = digitalRead(A_PHASE);  // Read current state of A phase
  int BState = digitalRead(B_PHASE);  // Read current state of B phase
  
  // Determine rotation direction based on quadrature signal changes
  if (AState != lastAState) {  // A phase state has changed
    if (AState == BState) {
      position++;  // Clockwise (CW) rotation
      flagB++;
    } else {
      position--;  // Counter-Clockwise (CCW) rotation
      flagA++;
    }
  } else if (BState != lastBState) {  // B phase state has changed
    if (AState != BState) {
      position++;  // Clockwise (CW) rotation
      flagB++;
    } else {
      position--;  // Counter-Clockwise (CCW) rotation
      flagA++;
    }
  }

  // Update last known states
  lastAState = AState;
  lastBState = BState;
}

void setup() {
  // Configure encoder input pins
  pinMode(A_PHASE, INPUT);
  pinMode(B_PHASE, INPUT);

  // Initialize encoder states
  lastAState = digitalRead(A_PHASE);
  lastBState = digitalRead(B_PHASE);

  // Initialize serial communication for debugging
  Serial.begin(115200);

  // Attach interrupts for encoder quadrature decoding
  attachInterrupt(digitalPinToInterrupt(A_PHASE), updateEncoder, CHANGE);
  attachInterrupt(digitalPinToInterrupt(B_PHASE), updateEncoder, CHANGE);

  // Connect to the VR setup's Wi-Fi network
  WiFi.hostname("Steering_ESP");
  WiFi.begin(ssid, password);

  // Wait for the Wi-Fi connection to be established
  while (WiFi.status() != WL_CONNECTED) {
    delay(1000);  // Retry connection every second
    Serial.println("Connecting with WiFi");
  }

  // Start the UDP service
  udp.begin(localUdpPort);
}

void loop() {
  unsigned long currentMillis = millis();
  
  // Send data at regular intervals
  if (currentMillis - previousMillis >= interval) {
    previousMillis = currentMillis;

    // Calculate the absolute steering angle from the encoder position
    float newAngle = (position * degrees_per_pulse);

    // Apply hysteresis filtering to reduce noise in updates
    if (abs(newAngle - lastAngle) >= hysteresisThreshold) {
      angle = newAngle;
      lastAngle = newAngle;
    }

    // Prepare JSON data containing the steering angle
    StaticJsonDocument<500> doc;
    String jsonStr;
    doc["sensor"] = "PHOTO_INCREMENT";  // Identifier for the steering sensor
    doc["angle"] = angle;  // Steering angle in degrees

    serializeJson(doc, jsonStr);

    // Send the JSON data to the main VR PC via UDP
    udp.beginPacket("192.168.0.101", localUdpPort);
    udp.print(jsonStr);
    udp.endPacket();

    // Debugging: Print the current steering angle to the Serial Monitor
    Serial.print("Absolute Angle: ");
    Serial.println(angle);
  }
}

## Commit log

2023-12-22 wrote batch and shell scripts to automatically execute the scripts, and implemented the steering for the rizer
2023-12-22 implemented script to write resistance level on direto
2024-02-09 edit scripts to use the raspberry pi 5 - next challenge dynamically use headwind without crashing the direto script
2024-02-21 editing run process; currently run on windows computer by executing batch script
2024-02-28 edit print statement for debugging purpose
2024-04-04 added folder with sensor scripts for the esp32
2024-05-14 seems it works. some errors in to send steerign to UDP calss
2024-07-01 incline works. steering method call is wrong
2024-09-09 ble reverse Eng. Comparing Rizer value for different steering angles.
2024-10-18 update steering Angle
2024-10-19 added Steering Sensor Platformio Repo
2024-10-23 add config for steering angle sensor
2024-11-11 init RTS Rotation Sensor Project
2024-11-25 initialize rotation sensor with dummy values
2024-12-19 added pedal sensor to esp32
2024-12-19 added pedal sensor to master_collector script
2024-12-19 version 2 of rotation sensor script
2024-12-20 changed number of magnets
2024-12-20 delay test for sensor version 2
2025-02-03 renamed backwheel sensor name
2025-04-30 Update of Brake Sensor Script
2025-05-08 update Gyro (Roll Sensor) Code and Setup
2025-05-19 minor update to code of backward motion sensor
2025-05-21 minor (cosmetic) updates of the code for the sensors: brake, gyro, roll and steering
2025-05-21 added all CAD files of recent updates to setup
    [GyroRollBoxLid.FCStd, GyroRollBoxLidStep.step, GyroRollBoxLidStl.stl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]
